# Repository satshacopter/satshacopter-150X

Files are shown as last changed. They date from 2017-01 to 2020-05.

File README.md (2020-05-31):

<h1 style="font-family: courier;" align="center">satshacopter 150X</h1>
<p align="center">
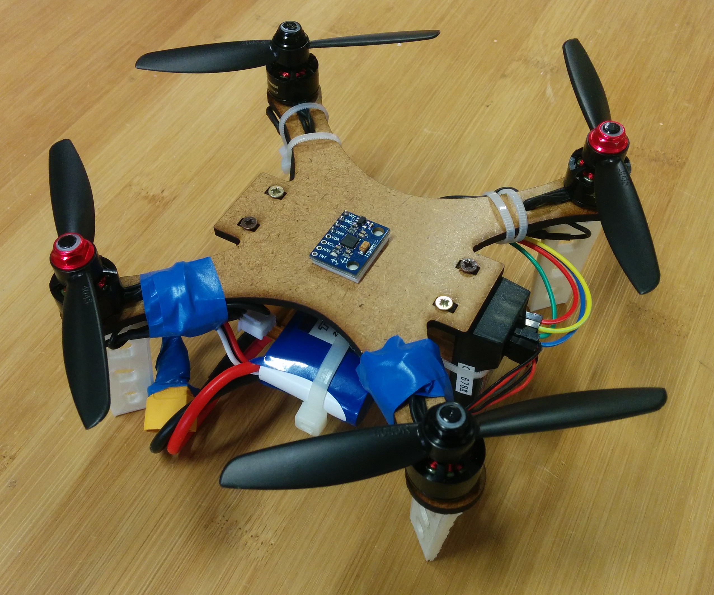
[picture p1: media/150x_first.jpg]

<div align="center"><i>An open source,small, low cost and fabbable quad X drone.</i></div>
</p>  

satshacopter 150X
--

satshacopter 150X is a quadcopter built around the **[satshakit mini flight controller](https://github.com/satshakit/satshakit-mini-flight-controller)** and derived from its big brother **[satshacopter 250X](https://github.com/satshacopter/satshacopter-250X)**. It is designed to be **simple and cheap as much as possible**, and to be easily made inside any **Fab Lab**.

150X specifications:

- **150mm mdf frame** and supports
- **open source flight controller**
- **MPU6050 IMU** located exactly at the center
- 4 x 3100kv **brushless motors**
- 4 x 6A **ESCs**
- **MultiWii** compatible
- Hobby King 4 channel **remote and receiver**
- 1000mah 2S 65C **LiPo battery** 
- costs around **100€**

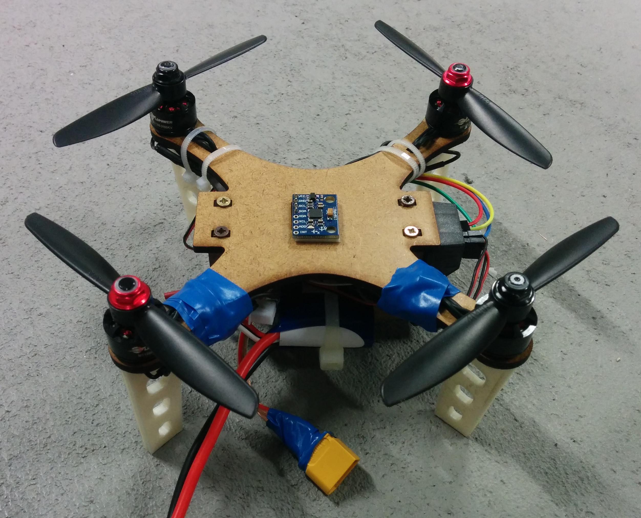
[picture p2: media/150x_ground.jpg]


Here you can look about the **MultiWii pin mapping** of the satshakit mini flight controller board:

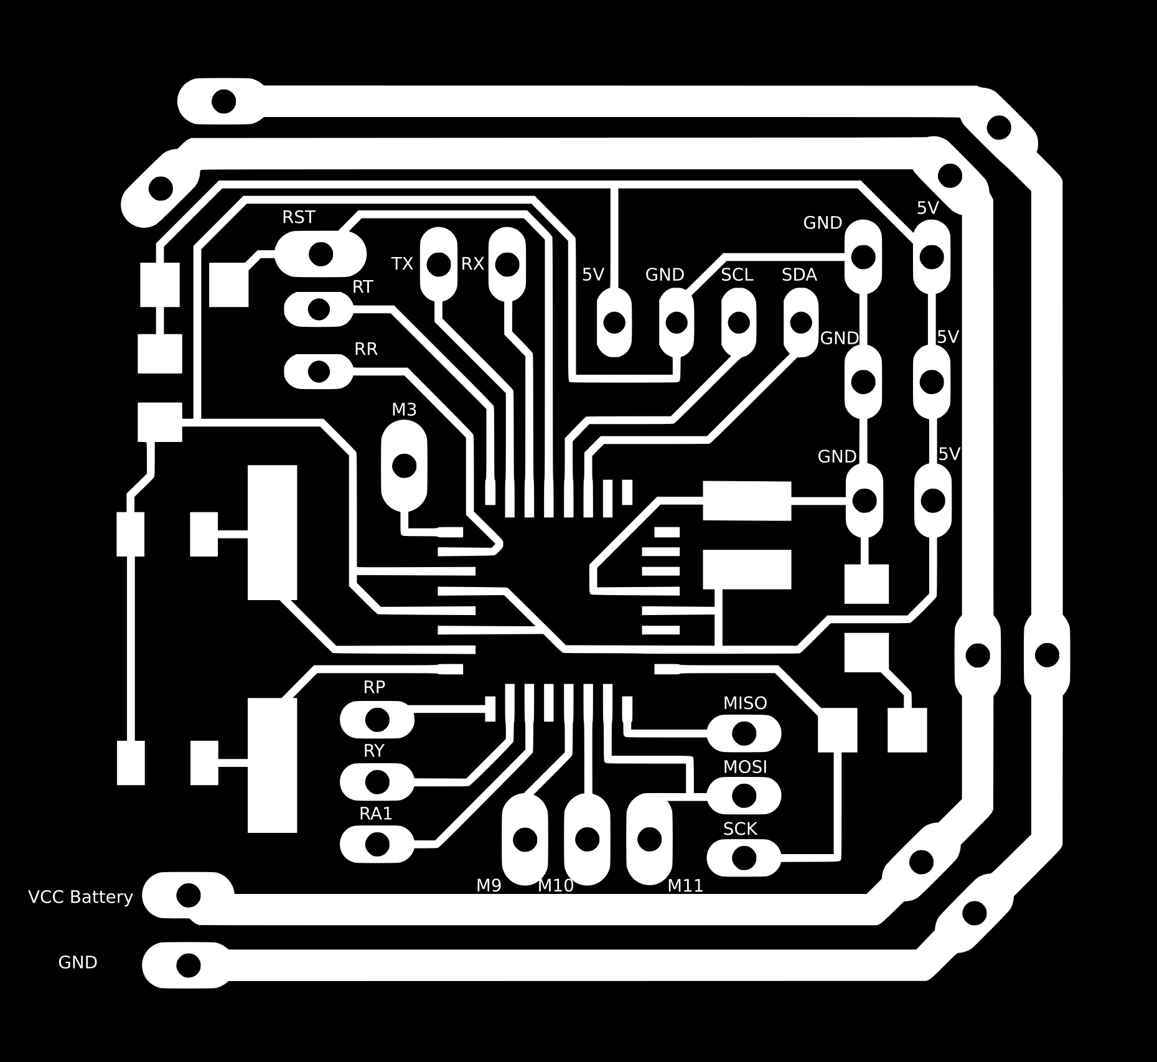
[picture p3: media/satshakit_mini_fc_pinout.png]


And here you can che the required components in the **Bill of Material** table:

|name|description|vendor|link|price|notes|
|:---:| :---:|:---:|:---:|:---:|:---:|
|2.4Ghz4Ch TxRx V2|4ch mode 2 remote control and receiver|Hobby King|[link](http://www.hobbyking.com/hobbyking/store/__66499__Hobby_King_2_4Ghz_4Ch_Tx_Rx_V2_Mode_2_EU_Warehouse_.html)|23.14€|-|
|Turnigy Graphene|battery 1000mah 2s 65C|Hobby King|[link](https://hobbyking.com/en_us/graphene-1000mah-2s-65c-w-xt60.html)|8.42€|-|
|LDPOWER D150 Multicopter Power System|4 x MT1306-3100KV motors and 4 x 6A esc|Hobby King EU|[link](https://hobbyking.com/en_us/ldpower-d150-multicopter-power-system-mt1306-3100kv-4-x-4-5-4-pack.html)|59.26€|propellers Included|
|IMU 6DOF|MPU6050 Gyro + Acc IMU|Ebay|[link](http://www.ebay.de/itm/MPU-6050-GY-521-3-Achsen-Gyroskop-Accelerometer-Kreisel-Board-Sensor-Arduino-21-/121887579651)|5.39€|-|
|LiPo Charger and Balancer|800mah 3s LiPo charger|Hobby King|[link](http://www.hobbyking.com/hobbyking/store/uh_viewitem.asp?idproduct=77525)|6.99€|-|
|Fligh Controller|satshakit mini flight controller|various|[link](https://github.com/satshakit/satshakit-flight-controller)|4.00-8.00€|depending on the quantity|
||||**Total price**|103.2€+4/8€|-|

NOTE: prices may change over time on the respective vendors, and also it is highly dependand on the quantity of drones you want to make.

Downloads
--

If you want to build by yourself a satshacopter 150X, please download the detailed **satshacopter 250X build manual** as a reference guide:

- [satshacopter 250X detailed build manual](https://github.com/satshacopter/satshacopter-250X/raw/master/docs/250X/satshacopter-250x-building-manual.pdf)

Following you can find all the **design files** you need to make it:

- [satshakit mini flight controller eagle board](https://github.com/satshacopter/satshacopter-150X/raw/master/eagle_projects/satshakit_mini_flight_controller/satshakit_mini_fc.brd)
- [satshakit mini flight controller eagle sch](https://github.com/satshacopter/satshacopter-150X/raw/master/eagle_projects/satshakit_mini_flight_controller/satshakit_mini_fc.sch)
- [satshakit mini flight controller internal traces png](https://github.com/satshacopter/satshacopter-150X/raw/master/media/satshakit_mini_fc_internal.png)
- [satshakit flight controller cut png](https://github.com/satshacopter/satshacopter-150X/raw/master/media/satshakit_mini_fc_cut.png)
- [mini frame and supports Rhino](https://github.com/satshacopter/satshacopter-150X/raw/master/design_files/frame_and_supports_3mm.3dm)
- [mini frame dxf](https://github.com/satshacopter/satshacopter-150X/raw/master/design_files/frame.dxf)
- [mini supports dxf](https://github.com/satshacopter/satshacopter-150X/raw/master/design_files/supports.dxf)
- [mini foot Rhino](https://github.com/satshacopter/satshacopter-150X/raw/master/design_files/foot.3dm)
- [mini foot STL](https://github.com/satshacopter/satshacopter-150X/raw/master/design_files/foot.stl)

Media
--

Some images of a satshacopter 150X:

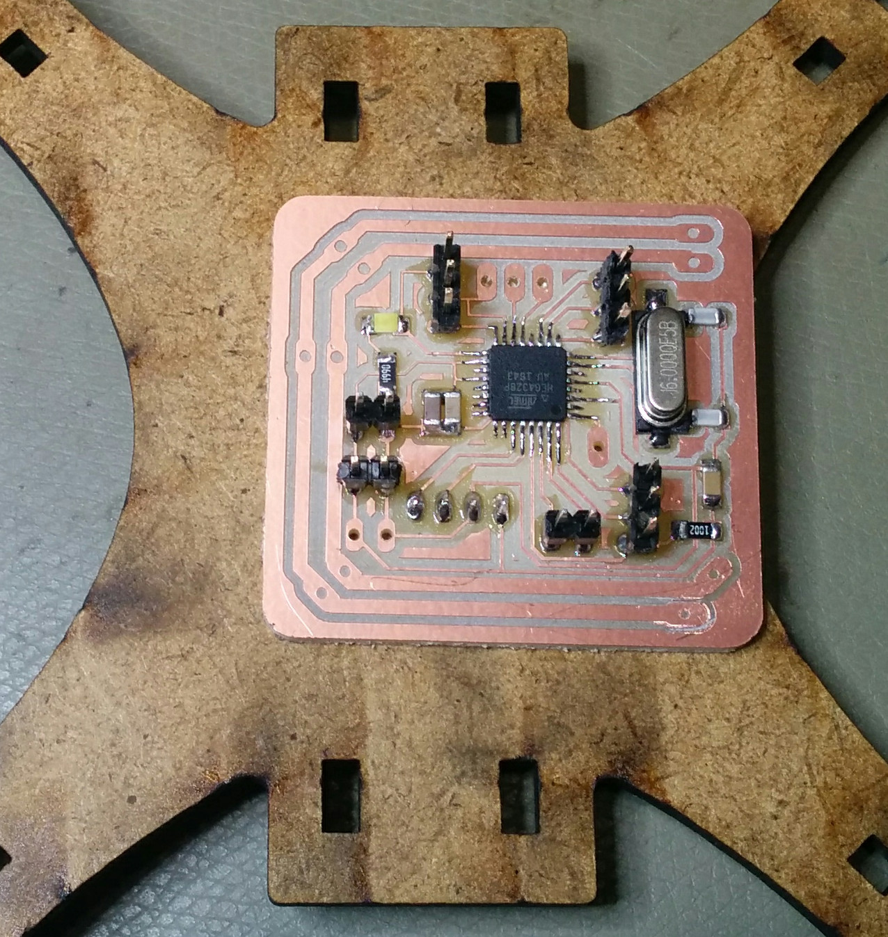
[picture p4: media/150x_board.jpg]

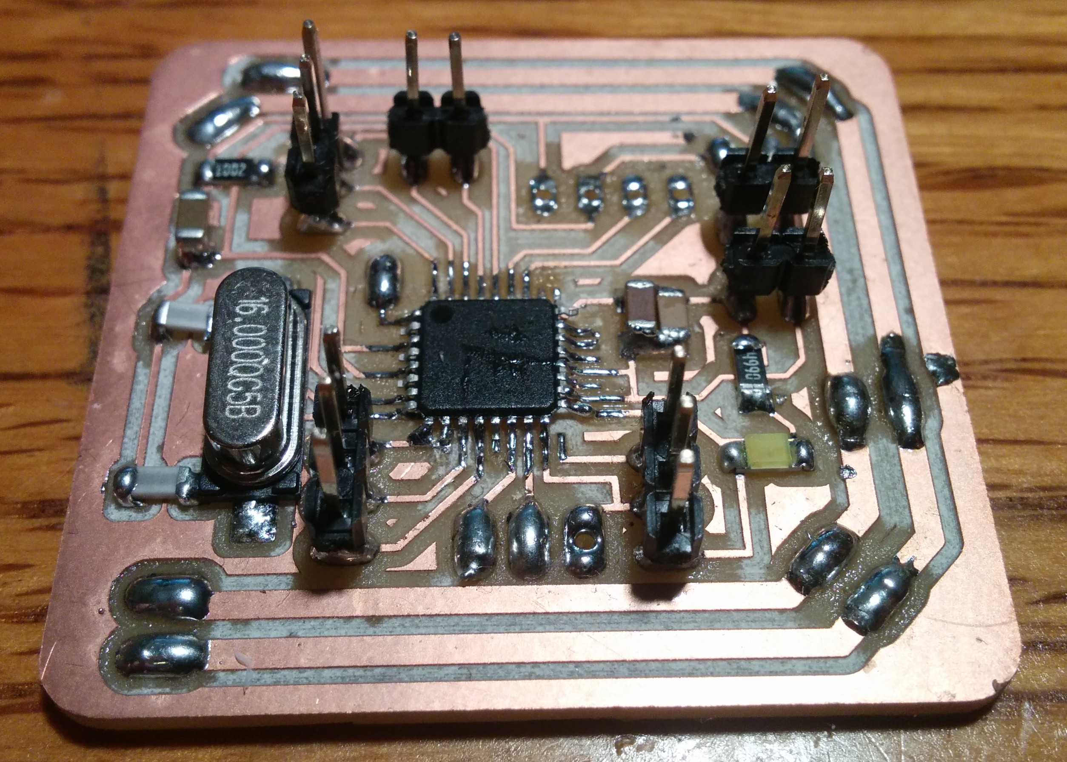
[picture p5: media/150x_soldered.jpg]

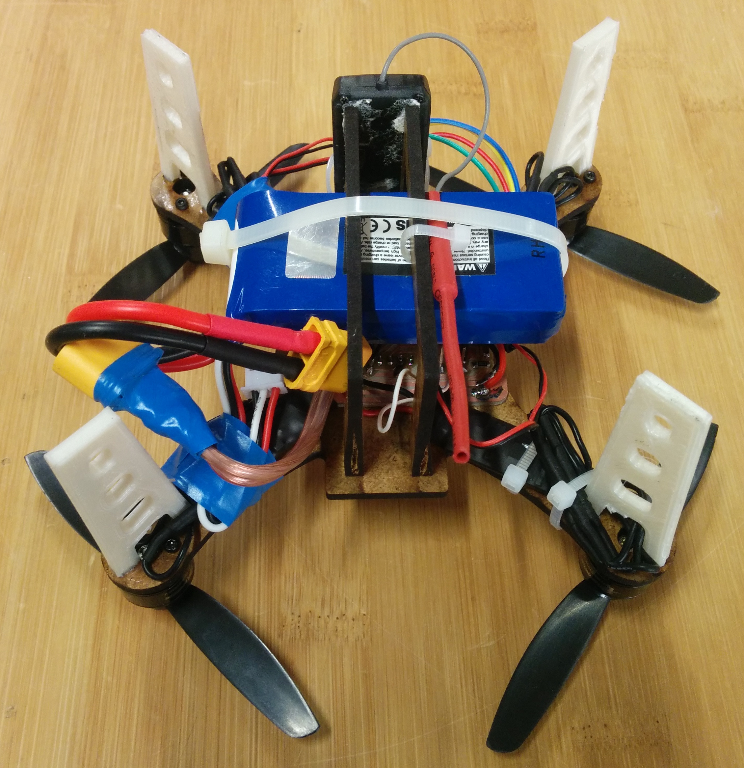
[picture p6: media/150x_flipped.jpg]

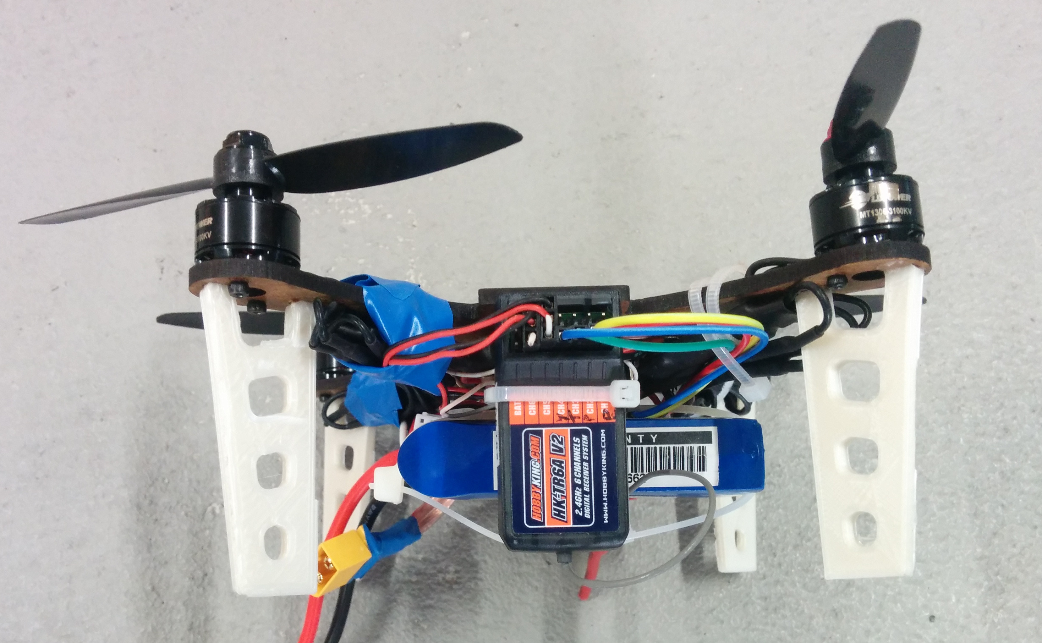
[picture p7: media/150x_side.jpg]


Safety
--

Please try always to fly safe.

Here are my personal safety recommendations, especially for experimental drones of which you are not sure on how they can behave:

- make sure to always keep an HUGE distance between you and the drone
- always place yourself on the back of the drone before starting flying
- always have the direct sight to the drone and make sure that its orientation is clear for you (use different colors or LEDs)
- fly in private areas where no public can access
- make sure that nobody can come near the drone while you are flying
- make sure that you cannot destroy anything that you have around you with the drone
- check the wind and the weather before flying, if outdoor
- never go too high (no more than 1/2 meters in these cases)
- do not fly on top of someone (neither yourself)
- first try to fly few cm above the ground to see if everything is correct
- try to avoid using carbon fiber props (they are really like rotating knifes) but use plastic props
- try to use smaller drones with smaller props for really experimental tests
- triple check all the screws and that the frame is not cracked somewhere
- triple check all the DIY electronics, if it fails in-flight can be extremely dangerous
- make sure that the batteries are full charged (both transmitter and the LiPos)

Authors
--

- Daniele Ingrassia

Contact
--

- **ingrassiada@gmail.com**
- **[linkedin](http://it.linkedin.com/in/danieleingrassia)**

Thanks
--

Aldo Sollazzo<br />
[Noumena](http://noumena.io/)<br />
Carrer de Pere IV 29-35, 4-1, Poblenou, 08018, Barcelona, Spain<br />
t: (+34) 652964886<br />
aldo@noumena.io <br />

[Fablab Kamp-Lintfort](http://fablab.hochschule-rhein-waal.de/index.php/de/)<br />
Hochschule Rhein-Waal<br />
Friedrich-Heinrich-Allee 25, 47475 Kamp-Lintfort, Germany<br />
fablab@hochschule-rhein-waal.de

License
--

This work is licensed under the terms of the open source license: Creative Commons Attribution-ShareAlike 4.0 International ([CC BY-SA 4.0](https://creativecommons.org/licenses/by-sa/4.0/)).

Disclaimer  
--

<div class="align-justify">
This hardware/software is provided "as is", and you use the hardware/software at your own risk. Under no circumstances shall any author be liable for direct, indirect, special, incidental, or consequential damages resulting from the use, misuse, or inability to use this hardware/software, even if the authors have been advised of the possibility of such damages.</div>

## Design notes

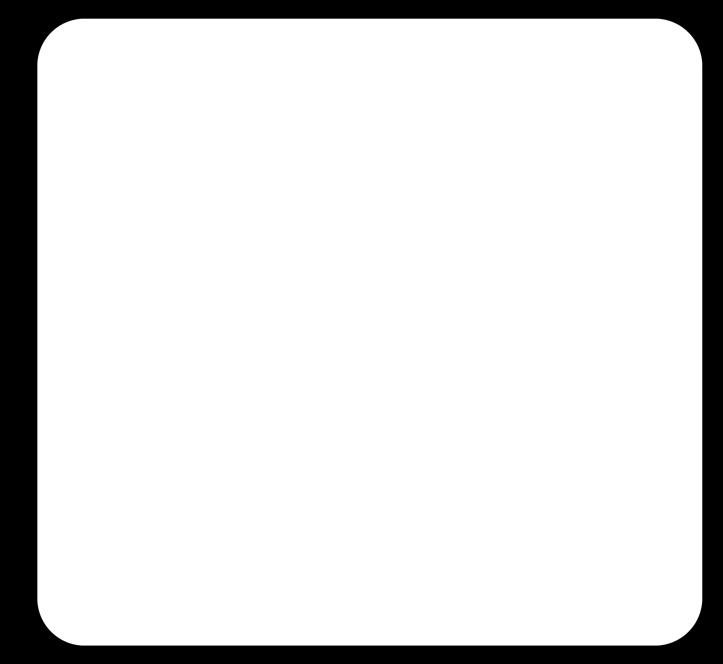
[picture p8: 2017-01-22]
media/satshakit_mini_fc_cut.png

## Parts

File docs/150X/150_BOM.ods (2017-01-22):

Name | Description | Vendor | Link | Unit Price
2.4Ghz4Ch TxRx V2 | 4ch mode 2 remote control and receiver | Hobby King EU | link (http://www.hobbyking.com/hobbyking/store/__66499__Hobby_King_2_4Ghz_4Ch_Tx_Rx_V2_Mode_2_EU_Warehouse_.html) | 23.14
Turnigy Graphene | battery 1000mah 2s 65C | Hobby King EU | link (https://hobbyking.com/en_us/graphene-1000mah-2s-65c-w-xt60.html) | 8.42
LDPOWER D150 Multicopter Power System | 4 x MT1306-3100KV motors and 4 x 6A esc | Hobby King EU | link (https://hobbyking.com/en_us/ldpower-d150-multicopter-power-system-mt1306-3100kv-4-x-4-5-4-pack.html) | 59.26
IMU 6DOF | MPU6050 Gyro + Acc IMU | Ebay (local) | link (http://www.ebay.de/itm/MPU-6050-GY-521-3-Achsen-Gyroskop-Accelerometer-Kreisel-Board-Sensor-Arduino-21-/121887579651) | 5.39
LiPo Charger and Balancer | 800mah 3s LiPo charger | Hobby King EU | link (http://www.hobbyking.com/hobbyking/store/uh_viewitem.asp?idproduct=77525) | 6.99
Frame | 3mm mdf frame | Local | - | 1.00
Fligh Controller | satshakit mini flight controller | Various | - | 8.00
Copper sheet | FR4 80 x 160 | Various | - | 1.00
Battery connectors | XT 60 female connectors | Hobby King EU | link (http://www.hobbyking.com/hobbyking/store/__36304__Female_XT60_Connectors_5pcs_bag_GENUINE_EU_Warehouse_.html) | 0.58
AA Batteries for the remote | 8 x AA 1.5V batteries | Local | - | 1.00
 |  |  |  | Price of the drone without shipping
 |  |  |  | 114.78

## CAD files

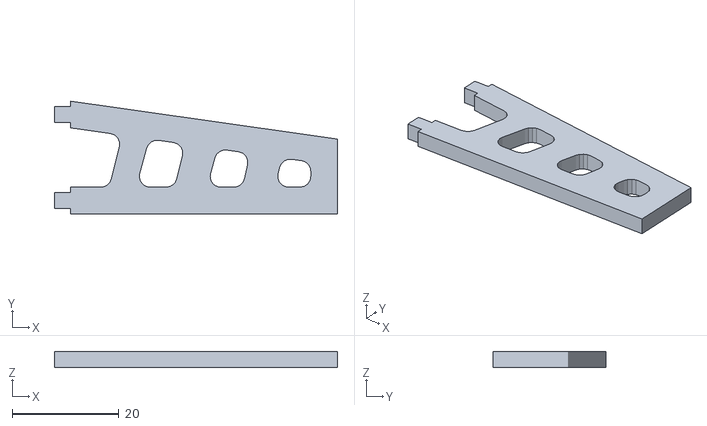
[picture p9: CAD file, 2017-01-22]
design_files/foot.stl
53.0 x 21.1 x 3.00

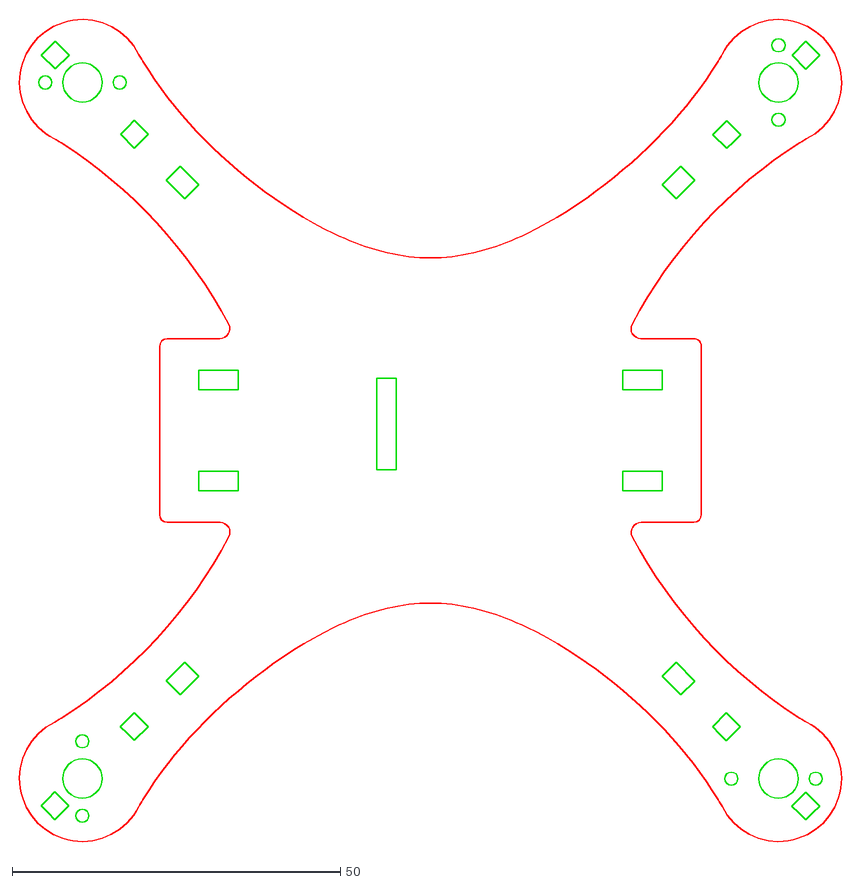
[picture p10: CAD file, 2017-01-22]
design_files/frame.dxf
126.3 x 126.3

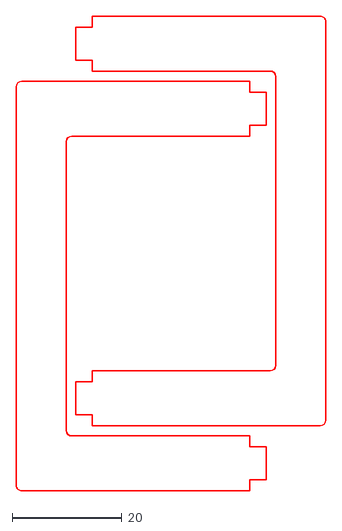
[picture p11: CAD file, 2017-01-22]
design_files/supports.dxf
56.4 x 86.4

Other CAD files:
design_files/foot.3dm
design_files/frame_and_supports_3mm.3dm

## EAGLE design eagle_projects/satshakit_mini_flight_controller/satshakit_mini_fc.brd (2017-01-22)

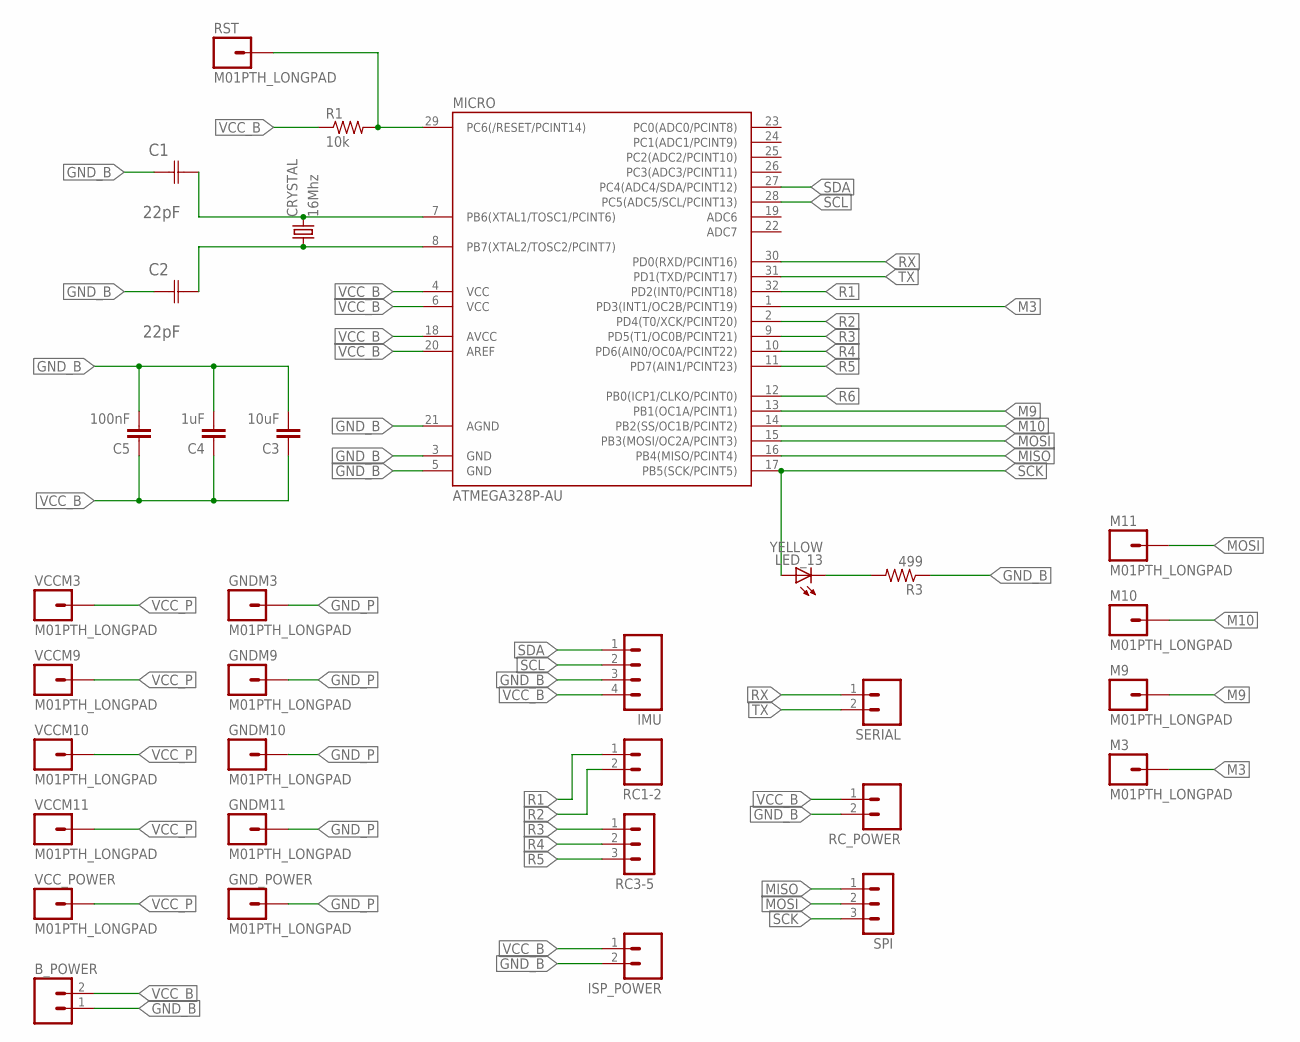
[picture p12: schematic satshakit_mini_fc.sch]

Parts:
B_POWER: M02LOCK_LONGPADS; 1X02_LOCK_LONGPADS
C1, C2: 22pF; CAPC3216X178N
C3: 10uF; 1206
C4: 1uF; 1206
C5: 100nF; 1206
CRYSTAL: 16Mhz; CSM-7X-DU
GNDM3, GNDM9, GNDM10, GNDM11: M01PTH_LONGPAD; 1X01_LONGPAD
GND_POWER: M01PTH_LONGPAD; 1X01_LONGPAD
IMU: M04; 04P
ISP_POWER: M02LOCK_LONGPADS; 1X02_LOCK_LONGPADS
LED_13: YELLOW; 1206
M3, M9, M10, M11: M01PTH_LONGPAD; 1X01_LONGPAD
MICRO: ATMEGA328P-AU; TQFP32-08
R1: 10k; 1206
R3: 499; 1206
RC1-2: M02; 02P
RC3-5: MA03-1
RC_POWER: M02LOCK_LONGPADS; 1X02_LOCK_LONGPADS
RST: M01PTH_LONGPAD; 1X01_LONGPAD
SERIAL: M02LOCK_LONGPADS; 1X02_LOCK_LONGPADS
SPI: MA03-1
VCCM3, VCCM9, VCCM10, VCCM11: M01PTH_LONGPAD; 1X01_LONGPAD
VCC_POWER: M01PTH_LONGPAD; 1X01_LONGPAD

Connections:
GND_B: B_POWER.1, C1.1 (C1), C2.1 (C1), C3.2, C4.2, C5.2, IMU.3, ISP_POWER.2, MICRO.3 (GND), MICRO.5 (GND), MICRO.21 (AGND), R3.1, RC_POWER.2
GND_P: GNDM3.1, GNDM9.1, GNDM10.1, GNDM11.1, GND_POWER.1
M3: M3.1, MICRO.1 (PD3(INT1/OC2B/PCINT19))
M9: M9.1, MICRO.13 (PB1(OC1A/PCINT1))
M10: M10.1, MICRO.14 (PB2(SS/OC1B/PCINT2))
MISO: MICRO.16 (PB4(MISO/PCINT4)), SPI.1
MOSI: M11.1, MICRO.15 (PB3(MOSI/OC2A/PCINT3)), SPI.2
unnamed: C1.2 (C2), CRYSTAL.2, MICRO.7 (PB6(XTAL1/TOSC1/PCINT6))
unnamed: MICRO.29 (PC6(/RESET/PCINT14)), R1.2, RST.1
unnamed: C2.2 (C2), CRYSTAL.1, MICRO.8 (PB7(XTAL2/TOSC2/PCINT7))
unnamed: LED_13.2 (C), R3.2
R1: MICRO.32 (PD2(INT0/PCINT18)), RC1-2.1
R2: MICRO.2 (PD4(T0/XCK/PCINT20)), RC1-2.2
R3: MICRO.9 (PD5(T1/OC0B/PCINT21)), RC3-5.1
R4: MICRO.10 (PD6(AIN0/OC0A/PCINT22)), RC3-5.2
R5: MICRO.11 (PD7(AIN1/PCINT23)), RC3-5.3
R6: MICRO.12 (PB0(ICP1/CLKO/PCINT0))
RX: MICRO.30 (PD0(RXD/PCINT16)), SERIAL.1
SCK: LED_13.1 (A), MICRO.17 (PB5(SCK/PCINT5)), SPI.3
SCL: IMU.2, MICRO.28 (PC5(ADC5/SCL/PCINT13))
SDA: IMU.1, MICRO.27 (PC4(ADC4/SDA/PCINT12))
TX: MICRO.31 (PD1(TXD/PCINT17)), SERIAL.2
VCC_B: B_POWER.2, C3.1, C4.1, C5.1, IMU.4, ISP_POWER.1, MICRO.4 (VCC), MICRO.6 (VCC), MICRO.18 (AVCC), MICRO.20 (AREF), R1.1, RC_POWER.1
VCC_P: VCCM3.1, VCCM9.1, VCCM10.1, VCCM11.1, VCC_POWER.1

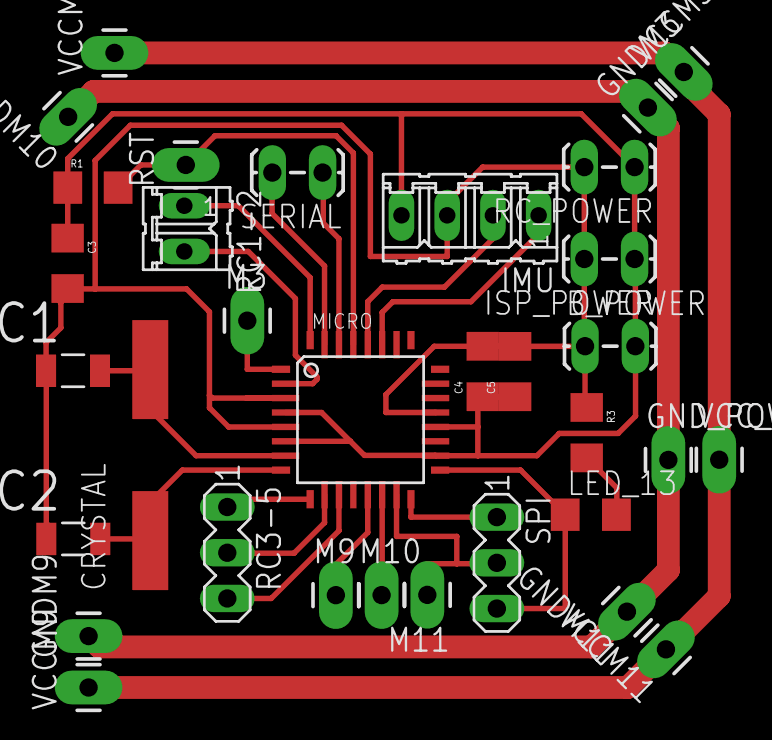
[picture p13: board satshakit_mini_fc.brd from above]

Board: 2 copper layers, 33 parts (0 on the bottom side), 23 nets.

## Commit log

2017-01-22 added some data
    [150X_DOM.xlsx, 150_BOM.ods, satshakit_mini_fc.brd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]
2017-01-22 added design files
    [foot.3dm, foot.stl, frame.dxf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]
2017-01-22 added png of the board

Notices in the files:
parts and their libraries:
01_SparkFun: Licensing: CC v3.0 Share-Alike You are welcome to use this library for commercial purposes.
